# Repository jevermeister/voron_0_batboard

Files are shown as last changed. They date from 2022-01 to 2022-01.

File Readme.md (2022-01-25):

# Batboard

The batboard is a passive tool board mounting on the back of the MiniAB pancake 
stepper of the Voron 0.1. The board solidly mounts with 20mm brass standoffs to the 
back of the mini after burner mounting screws and provides JST PH connectors 
(2mm pitch) for the two part cooling fans, the hotend fan, a 4-pin thermistor, 
two switches (for example the X endstop + a klicky probe) as well as the stepper and a chamber thermistor. 
The heater output is provided as a 2x1 Molex Microfit connector and all terminals 
are terminated onto a 2x9 Microfit.

# BOM

For the PCB:
- 1x Molex 43045-1800 (Microfit 2x9) 
- 1x Molex 43045-0200 (Microfit 2x1)
- 3x JST PH 2 Pin, B2B-PH-K-S(LF)(SN)
- 3x JST PH 3 Pin, B3B-PH-K-S(LF)(SN)
- 2x JST PH 4 Pin, B4B-PH-K-S(LF)(SN)
- MF58 3950 thermistor

And the appropriate connectors for your cable loom...

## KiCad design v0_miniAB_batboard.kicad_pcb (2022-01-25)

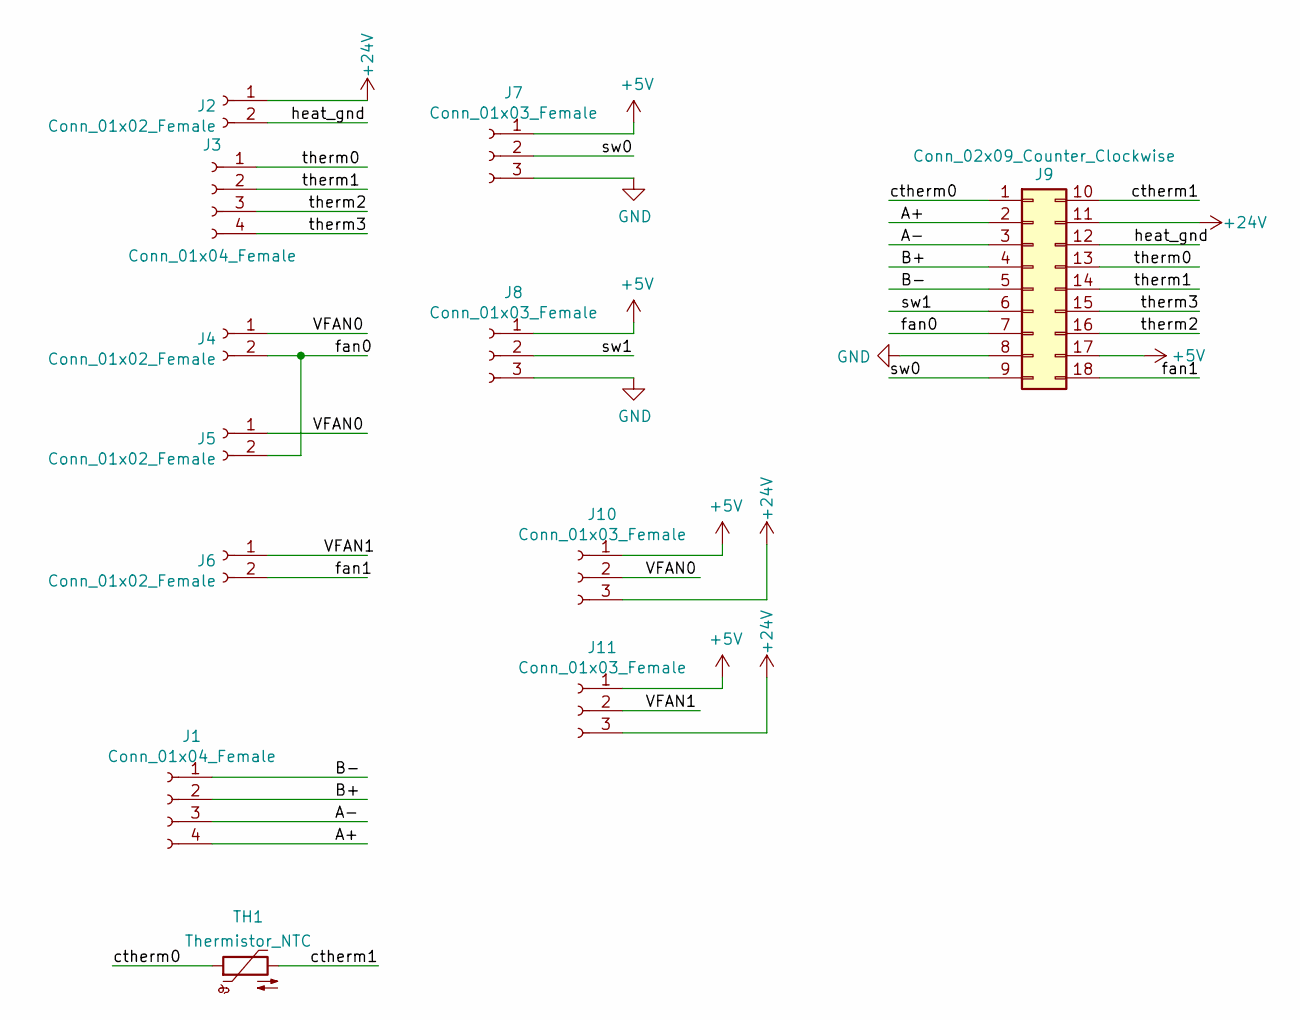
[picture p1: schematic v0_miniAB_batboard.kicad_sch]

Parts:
J1, J3: Conn_01x04_Female; JST_PH_B4B-PH-K_1x04_P2.00mm_Vertical
J2: Conn_01x02_Female; Molex_Micro-Fit_3.0_43045-0200_2x01_P3.00mm_Horizontal
J4, J5, J6: Conn_01x02_Female; JST_PH_B2B-PH-K_1x02_P2.00mm_Vertical
J7, J8: Conn_01x03_Female; JST_PH_B3B-PH-K_1x03_P2.00mm_Vertical
J9: Conn_02x09_Counter_Clockwise; Molex_Micro-Fit_3.0_43045-1800_2x09_P3.00mm_Horizontal
J10, J11: Conn_01x03_Female; SolderJumper-3_P1.3mm_Bridged12_RoundedPad1.0x1.5mm_NumberL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
TH1: Thermistor_NTC; R_Axial_DIN0204_L3.6mm_D1.6mm_P7.62mm_Horizontal

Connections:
+5V: J7.1, J8.1, J9.17, J10.1, J11.1
+24V: J2.1, J9.11, J10.3, J11.3
/A+: J1.4, J9.2
/A-: J1.3, J9.3
/B+: J1.2, J9.4
/B-: J1.1, J9.5
/VFAN0: J4.1, J5.1, J10.2
/VFAN1: J6.1, J11.2
/ctherm0: J9.1, TH1.1
/ctherm1: J9.10, TH1.2
/fan0: J4.2, J5.2, J9.7
/fan1: J6.2, J9.18
/heat_gnd: J2.2, J9.12
/sw0: J7.2, J9.9
/sw1: J8.2, J9.6
/therm0: J3.1, J9.13
/therm1: J3.2, J9.14
/therm2: J3.3, J9.16
/therm3: J3.4, J9.15
GND: J7.3, J8.3, J9.8

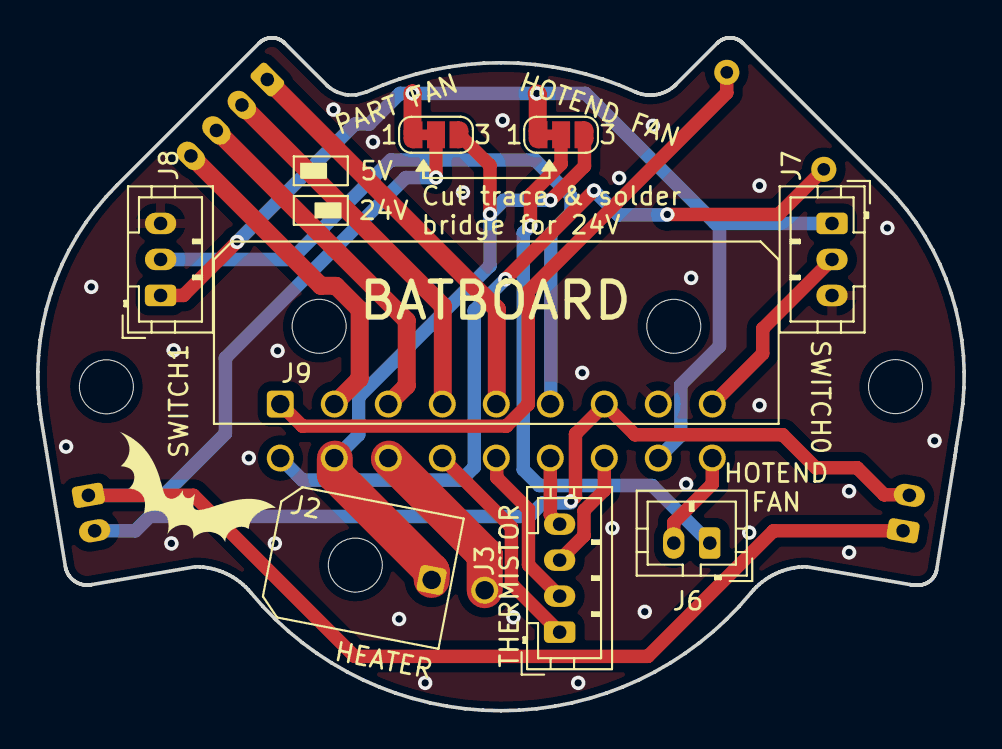
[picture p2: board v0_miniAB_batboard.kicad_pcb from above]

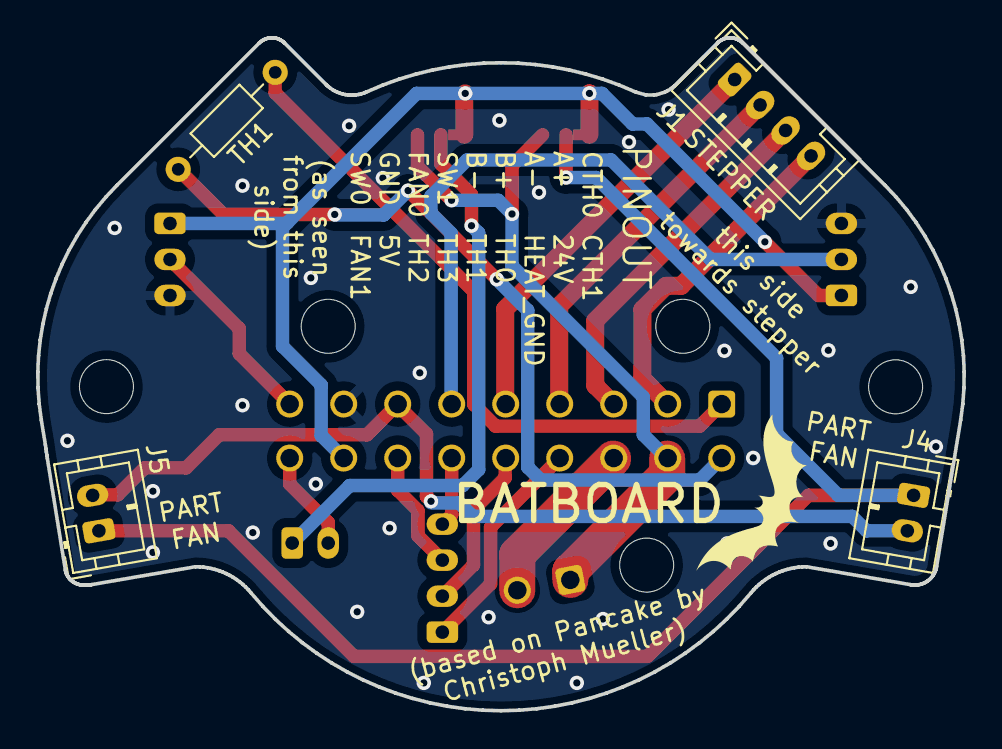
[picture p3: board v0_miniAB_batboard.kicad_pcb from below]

Board: 2 copper layers, 51.5 x 37.4 mm, 14 parts (5 on the bottom side), 20 nets.

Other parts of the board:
svg2mod, svg2mod#2: G***; Bat_Logo

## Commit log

2022-01-11 Converted to KiCAD 6.0.0
    [v0_miniAB_pancake_board.kicad_pcb, v0_miniAB_pancake_board.kicad_sch]
2022-01-21 First steps of the batboard conversion
    [v0_miniAB_pancake_board.kicad_pcb, v0_miniAB_pancake_board.kicad_sch]
2022-01-21 Further connections made
    [v0_miniAB_pancake_board.kicad_pcb, v0_miniAB_pancake_board.kicad_sch]
2022-01-21 Fixed track to VFAN1
    [v0_miniAB_pancake_board.kicad_pcb]
2022-01-21 Removed mini bat behind connector
    KSS KSSSSSS
    [v0_miniAB_pancake_board.kicad_pcb]
2022-01-25 Moved some things, added CT, checked clearance
    [v0_miniAB_pancake_board.kicad_pcb, v0_miniAB_pancake_board.kicad_sch]
2022-01-25 Removed unused files
    [v0_miniAB_pancake_board.sch, v0_miniAB_pancake_board.step]
2022-01-25 Renamed files
    [v0_miniAB_batboard.kicad_pcb, v0_miniAB_batboard.kicad_sch]
2022-01-25 Minor adjustments and added Gerber files
    [v0_miniAB_batboard-B_Cu.gbl, v0_miniAB_batboard-B_Mask.gbs, v0_miniAB_batboard-B_Paste.gbp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]
